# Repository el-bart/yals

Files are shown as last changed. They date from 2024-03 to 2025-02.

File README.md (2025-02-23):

# YALS: Yet Another Linear Servo

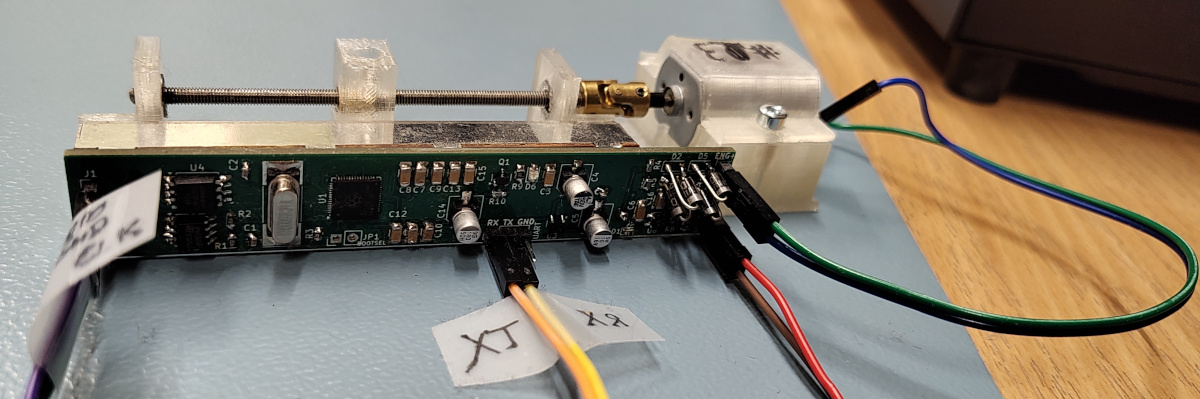
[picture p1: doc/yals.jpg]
YALS 1st prototype


project to build a linear servo for RC models.

## key project assumptions

* long move range
* digital position control
* digital feedback on current servo position
* 12V power supply (directly from battery)
* does not consume power when not moving, while still keeping position
* possible magnetic coupling with element moved
* programmable and persistent:
  * min / max positions
  * LED brightness

## building

TL;DR just run `make` from project's root directory.

toolchain has been dockerized.
to make usage more convenient, there's a top-level `Makefile` to run all the elements.
it automatically keeps dependsncies in place.

generated stuff:
* 3D models for printing:
  * all in: `body/build/voron_24_revo/petg/strength/*.gcode`
  * note that there can be >1 carriage to choose from
* electronics (HW):
  * gerber files for PCB: `board/hw/build/gerber.zip`
  * PCB assembly: `board/hw/build/graphics/`
  * BOM: `board/hw/build/bom.csv`
* software (SW):
  * to flash use `./rp2020_sdk rp2040_flash <name_of_binary.elf>` from `board/sw` directory
  * binaries:
    * controller to flash (production): `board/sw/build/rp2040/servo_ctrl.elf`
    * manual tests (for validation of HW assembly):
      * `board/sw/build/rp2040/Hal/rp2040/Hal_*.mtest.elf`
      * `board/sw/build/rp2040/Utils/*.mtest.elf`

## assembly

### BOM
* 1x PCB assembly (see `baord/hw` - build it to get `board/hw/build/bom.csv`)
* 1x MT44 DC motor
* 2x 3x7x3mm ball bearing
* 1x 3mm-3mm universal joing (aka: Cardan joint)
* 1x 3mm threaded rod (~12cm)
* 3x 3mm threaded inset (1x for carriage and 2x for engine)
* 2x M3x14 screws (engine mount)
* 2x M3x10 screws (potentiometer mount)

### tools
* soldering iron
* 3D printer for YALS' body
* hex-key set
* pico-probe or raspberry pi SBC to flash `rp2040` µC

## FAQ

### why no position-watchdog?
µC has internal watchdog, that kicks in in case software gets stuck.

however there's no application-level watchdog (e.g. a dedicated command that'd require a new command reception in a given time)
as servo does not go bonkers when signal is lost (as typical, cheap, analog do).
instead it keeps current position effortlessly.
on start, current position is retained as well.
therefor there's no need to perform any special actions, when no new command is received.

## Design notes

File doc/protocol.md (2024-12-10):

# protocol definition

communication protocol definition, used to communicate with the YALS device.
it consists of 1-line commands and responses and ends with checksum.
line ends with a new-line character (`\n` or `\r`).

consecutive new-line characters are ignored.

despite of being ASCII-printable, for ease of parsing, each command is fixed-width.
this means that values might need to be `0`-padded.

## checksum

checksum is calculated as a bit XOR of all bytes of the source frame.
checksum is hex-encoded.

example checksum of 3 bytes of data (here as hex): `0xFF 0x42 0x10`  is equal to:
`0xFF ^ 0x42 ^ 0x10`.
note that new-line characters are not part of checksum.

checksum is optional.
a literal string `XX` can be used to indicate it's not set and should not be checked.
this is mostly for debugging purposes - it should never be used in production!

## protocol

### ping
#### request
```
~XX\n
```
where:
* `XX` is hex-encoded checksum (or literal `XX` - meaning unset)
#### reply
* OK: `+msgXX\n` where:
  * `msg` is a string containing basic device info (name, version, etc.). 30B max.
  * `XX` is hex-encoded checksum
* error: `-msgXX\n` where:
  * `msg` is an error description string. 30B max.
  * `XX` is hex-encoded checksum

### set servo position
#### request
```
@nnnXX\n
```
where:
* `nnn` is servo position in 000..999 range
* `XX` is hex-encoded checksum (or literal `XX` - meaning unset)
#### reply
* OK: `+XX\n`
  * `XX` is hex-encoded checksum
* error: `-msgXX\n` where:
  * `msg` is a string containing basic device info (name, version, etc.). 30B max.
  * `XX` is hex-encoded checksum

### get servo position
#### request
```
!XX\n
```
where:
* `XX` is hex-encoded checksum (or literal `XX` - meaning unset)
#### reply
* OK: `+nnnXX\n` where:
  * `nnn` is a current 000..999 servo position
  * `XX` is hex-encoded checksum
* error: `-msgXX\n` where:
  * `msg` is a string containing basic device info (name, version, etc.). 30B max.
  * `XX` is hex-encoded checksum

### set min servo position
#### request
```
<nnnXX\n
```
where:
* `nnn` is 000...999 position
* `XX` is hex-encoded checksum (or literal `XX` - meaning unset)
#### reply
* OK: `+XX\n`
  * `XX` is hex-encoded checksum
* error: `-msgXX\n` where:
  * `msg` is a string containing basic device info (name, version, etc.). 30B max.
  * `XX` is hex-encoded checksum

### set max servo position
#### request
```
>nnnXX\n
```
where:
* `nnn` is 000...999 position
* `XX` is hex-encoded checksum (or literal `XX` - meaning unset)
#### reply
* OK: `+XX\n`
  * `XX` is hex-encoded checksum
* error: `-msgXX\n` where:
  * `msg` is a string containing basic device info (name, version, etc.). 30B max.
  * `XX` is hex-encoded checksum

### set LED brightness
#### request
```
*nnXX\n
```
where:
* `nn` is 00...99 LED brightness
* `XX` is hex-encoded checksum (or literal `XX` - meaning unset)
#### reply
* OK: `+XX\n`
  * `XX` is hex-encoded checksum
* error: `-msgXX\n` where:
  * `msg` is a string containing basic device info (name, version, etc.). 30B max.
  * `XX` is hex-encoded checksum

### get telemetry
#### request
```
#XX\n
```
where:
* `XX` is hex-encoded checksum (or literal `XX` - meaning unset)
#### reply
* OK: `+IiiiiUuuuuuXX\n` where:
  * `iiii` is current engine current in `mA` (0000..9999); e.g. `1234` is 1.234 A.
  * `uuuuu` is current main voltage in `mV` (00000..99999); e.g. `12345` is 12.345 V.
  * `XX` is hex-encoded checksum
* error: `-msgXX\n` where:
  * `msg` is a string containing basic device info (name, version, etc.). 30B max.
  * `XX` is hex-encoded checksum

### get persistent configuration
#### request
```
?XX\n
```
where:
* `XX` is hex-encoded checksum (or literal `XX` - meaning unset)
#### reply
* OK: `+<mmm>MMM*bbXX\n` where:
  * `mmm` is 000..999 servo min position
  * `MMM` is 000..999 servo max position
  * `bb` is 00..99 LED brightness
  * `XX` is hex-encoded checksum
* error: `-msgXX\n` where:
  * `msg` is a string containing basic device info (name, version, etc.). 30B max.
  * `XX` is hex-encoded checksum

### cheatsheet

this section is a brief summary of the whole section.
it's based on examples with 1-liner explanation.

all `XX` characters should be replaced with checksum, or can be taken literally (i.e. no checksum).
replies also ommit checksums.

* ping / get version info:
  * request: `~XX\n`
  * reply: `YALS v1.2.3-42-abcedfXX\n`
* set servo position to `98`
  * request: `@098XX\n`
  * reply: `+XX\n`
* return servo position (set to `098`)
  * request: `!XX\n`
  * reply: `+098XX\n`
* set servo minimum position to `200`:
  * request: `<200XX\n`
  * reply: `+XX\n`
* set servo maximum position to `800`:
  * request: `>800XX\n`
  * reply: `+XX\n`
* set LED birghtness to `42`:
  * request: `*42XX\n`
  * reply: `+XX\n`
* get telemetry:
  * request: `#XX\n`
  * reply: `+I01234U12345XX\n` (i.e. 0.1234 A and 12.345 V
* get persisted configuration:
  * request: `?XX\n`
  * reply: `+<200>800*42XX\n` (i.e. pos limits are 200..800, LED brightness is 42)

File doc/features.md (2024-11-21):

# features

## startup
* moving servo to within min..max range on init
* setting LED brightness

## protocol
* simple, ASCII-based serial protocol for I/O
* getting and setting:
  * servo position
  * min/max positions range for servo (preserved across restarts)
* readout:
  * SW information
  * telemetry (Vcc, engine current)

## misc
* hard min/max limits, compensating for potentiometer inaccuracies

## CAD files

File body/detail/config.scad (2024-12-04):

include <../m3d/engine/dc/mt44_conf.scad>

// CDE23N-60-B50K linear potentiometer (horizontal, on side, knob to the right)
lin_pot_travel = 60;
lin_pot_size = [11, lin_pot_travel+28.3, 13];
lin_pot_mount_screw_d = 3;
lin_pot_mount_screw_dist_from_edge = ( lin_pot_size.y - lin_pot_travel - 20 ) / 2;
lin_pot_mount_screw_pos = [4, lin_pot_size.y-4];
lin_pot_knob_size = [15.3, 5, 1.2];
lin_pot_knob_dist_from_edge = ( lin_pot_size.y - lin_pot_travel ) / 2;
lin_pot_knob_pos_range = [lin_pot_knob_dist_from_edge, lin_pot_size.y - lin_pot_knob_dist_from_edge];

// MT44 engine - mock sizes taken from m3d
engine_box_size = engine_dc_mt44_box_size;
engine_size_shaft_d = engine_dc_mt44_shaft_d;
engine_size_shaft_h = engine_dc_mt44_shaft_h + engine_dc_mt44_bearing_top_h;
engine_size_total_len = engine_box_size.z + engine_size_shaft_h;

// universal joint
universal_joint_part_bottom_h = 2.8;
universal_joint_part_top_h = 8.75;
universal_joint_part_joint_h = 6.5;
universal_joint_full_len = 2 * universal_joint_part_joint_h;
universal_joint_d = 7;
universal_joint_shaft_d = 3;
universal_joint_wall = 1;
assert( universal_joint_shaft_d + 2*universal_joint_wall <= universal_joint_d );
universal_joint_center_spacing = universal_joint_part_joint_h - universal_joint_part_bottom_h; // distance to be kept from the center of the joint

// screw row
screw_rod_d = 3;

// servo body
servo_body_bottom_h = 2;
servo_body_wall = 2;
servo_body_mount_screw_d = 3;
servo_body_threaded_insert_slot_d = 4.6;
servo_body_threaded_insert_slot_h = 5.7;
servo_body_engine_mount_spacing_r = 0.15; // around the engine
servo_body_engine_mount_spacing_h = 0.15; // before and after engine (dy)

// bearing size [mm]
bearing_size = [3, 7, 3]; // [ internal_d, external_d, h ]

// combined, utility metrics
base_to_axis_h = servo_body_bottom_h + lin_pot_size.z;

// servo body: mount tower dimensions
servo_body_mount_tower_hole_dist_to_wall = 3;
servo_body_mount_tower_size = ( servo_body_mount_screw_d + 2 * servo_body_mount_tower_hole_dist_to_wall ) * [1,1,0] +
                              [ 0,0, base_to_axis_h +
                                engine_box_size.y/2 +
                                servo_body_engine_mount_spacing_r +
                                servo_body_wall ];

// carriage
carriage_magnet_d = 5;
carriage_magnet_h = 5;
carriage_wall = 2;
carriage_knob_slot_spacing = 0.5;
carriage_rod_h = carriage_wall + (carriage_knob_slot_spacing + lin_pot_knob_size.z)/2 + // center to potentiometer's knob center
                 base_to_axis_h - servo_body_bottom_h - lin_pot_size.z/2;               // move to height of the rod
carriage_size = [ 10,
                  lin_pot_knob_size.y + 2*carriage_wall,
                  carriage_rod_h + screw_rod_d/2 + carriage_wall + carriage_magnet_h ];
carriage_threaded_insert_slot_d = 4.6;
carriage_threaded_insert_slot_h = 5.7;

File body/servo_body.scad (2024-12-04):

use <mock/lin_pot.scad>
use <mock/bearing.scad>
use <mock/universal_joint.scad>
use <mock/pcb.scad>
use <servo_body_top_mount.scad>
use <carriage.scad>
use <m3d/fn.scad>
use <m3d/engine/dc/mt44.scad>
include <m3d/math.scad>
include <detail/config.scad>

module engine()
{
  engine_dc_mt44();
}

module engine_crosssecion_2d()
{
  engine_dc_mt44_crosssection_2d();
}


module servo_body_engine_pos()
{
  translate([0, -engine_size_total_len - universal_joint_center_spacing, base_to_axis_h]) // axis-centered
    rotate([-90, 0, 0])
      children();
}


module servo_body_lin_pot_pos()
{
  translate([0, 0, servo_body_bottom_h])
    translate([-lin_pot_knob_size.x/2, 0, -lin_pot_size.z/2]) // mount position
      translate([-lin_pot_size.x, 0, lin_pot_size.z/2]) // axis-centered
        children();
}


module servo_body_pcb_pos()
{
  translate([-5, -14.3, -servo_body_bottom_h+1])
    servo_body_lin_pot_pos()
      children();
}


module servo_body_universal_joint_pos()
{
  translate([0, -universal_joint_full_len/2, base_to_axis_h])
    rotate([-90, 0, 0])
      children();
}


module servo_body_carriage_pos()
{
  knob_center = lin_pot_knob_pos_range[0] + (lin_pot_knob_pos_range[1] - lin_pot_knob_pos_range[0]) / 2;
  translate([ lin_pot_size.x + lin_pot_knob_size.x/2,
              knob_center,
              lin_pot_size.z/2 - lin_pot_knob_size.z/2 - carriage_wall - carriage_knob_slot_spacing/2 ]) // move to final spot
    translate([-carriage_size.x/2, -carriage_size.y/2, 0]) // center
      servo_body_lin_pot_pos()
        children();
}


module servo_body_mount_tower_center_pos()
{
  w = servo_body_mount_tower_size.x;

  // around engine
  sbw = servo_body_wall;
  screw_mount_space = sbw + servo_body_threaded_insert_slot_d + sbw;
  engine_base_plate_y = engine_size_total_len + universal_joint_center_spacing + sbw;
  for(dx=[-1, +1])
    translate([ dx*(engine_box_size.x + 2*screw_mount_space)/2,
                -engine_base_plate_y + sbw,
                0 ])
      translate([dx*w/2, w/2, 0])
        children();

  // end of cariage
  for(dx=[-1, +1])
    translate([dx*w/2, lin_pot_size.y, 0])
      translate([0, w/2, 0])
        rotate([0, 0, 90])
          children();
}


module servo_body(mocks=true)
{
  module mount_tower()
  {
    d2w = servo_body_mount_tower_hole_dist_to_wall;
    size = servo_body_mount_tower_size;
    w = size.x;
    assert(size.x == size.y);
    h = size.z;

    translate(-w/2*[1,1,0])
      difference()
      {
        $fn=fn(30);
        ssd = servo_body_mount_screw_d + 0.5; // screw slot diameter

        cube(size);
        // top-down screw
        translate([w/2, w/2, -eps])
          cylinder(d=ssd, h=h+2*eps);
        // front-back screws (top and bottom)
        translate([0, -eps, 0])
          rotate([-90, 0, 0])
            for(dy=[ssd/2 + d2w, h - ssd/2 - d2w])
              translate([w/2, -dy, 0])
                cylinder(d=ssd, h=w+2*eps);
      }
  }

  module main_support()
  {
    lps = lin_pot_size;
    ks = lin_pot_knob_size;
    bh = servo_body_bottom_h;
    thickness = 3.5;

    module lin_pot_screw_mounts()
    {
      module blocks()
      {
        module lin_pot_screw_mount()
        {
          s = [thickness, lin_pot_knob_pos_range[0]-lin_pot_knob_size.y/2, lin_pot_size.z];

          module phased_cube(size, phase)
          {
            translate([0, size.y, 0])
              rotate([90, 0, 0])
                linear_extrude(size.y)
                  polygon([
                    [0, 0],
                    [0, size.z],
                    [size.x - phase[0], size.z],
                    [size.x,            size.z - phase[1]],
                    [size.x, 0],
                  ]);
          }

          phased_cube(size=s, phase=[2/3*s.x, s.x]);
        }

        for(dy=[0, lin_pot_knob_pos_range[1]+ks.y/2])
          translate([lin_pot_size.x, dy, 0])
            servo_body_lin_pot_pos()
              lin_pot_screw_mount();
      }

      difference()
      {
        blocks();
        // screw holes
        for(dy=lin_pot_mount_screw_pos)
          translate([-eps+lin_pot_size.x, dy, lin_pot_size.z/2])
            servo_body_lin_pot_pos()
              rotate([0, 90, 0])
                cylinder(d=lin_pot_mount_screw_d+0.75, h=thickness+2*eps, $fn=fn(50));
      }
    }

    module bearing_support()
    {
      h = base_to_axis_h - servo_body_bottom_h + bearing_size[1]/2 + thickness;
      s = [lin_pot_knob_size.x, thickness, h];
      pos = lin_pot_knob_pos_range + [-s.y-lin_pot_knob_size.y/2, lin_pot_knob_size.y/2];

      module support()
      {
        difference()
        {
          cube(s);
          translate([s.x/2, -eps, base_to_axis_h-servo_body_bottom_h])
          {
            // rod
            rotate([-90, 0, 0])
              cylinder(d=screw_rod_d+1, h=s.y+2*eps, $fn=fn(40));
            rotate([-90, 0, 0])
              bearing_slot();
          }
        }
      }

      translate([-s.x/2, 0, servo_body_bottom_h])
      {
        // supports
        for(dy=pos)
          translate([0, dy, 0])
            support();
        // stiffners
        ss = [thickness, pos[1]-pos[0], thickness/2];
        for(dx=[0, s.x-ss.x])
          translate([dx, pos[0], 0])
            cube(ss);
      }
    }

    module engine_support()
    {
      wall = servo_body_wall;
      es = [ engine_box_size.x, engine_box_size.z, engine_box_size.y ];
      screw_mount_space = wall + servo_body_threaded_insert_slot_d + wall;
      sb = [ es.x + 2*screw_mount_space,
             engine_size_total_len + universal_joint_center_spacing + wall,
             servo_body_bottom_h ];

      module base_engine_mount()
      {
        to_eng_base = base_to_axis_h - servo_body_bottom_h - es.z/2;
        eng_sup = [ sb.x, es.y, base_to_axis_h - servo_body_bottom_h ];

        module support_block()
        {
          module core()
          {
            // engine block holder
            translate([0, wall, 0 ])
            {
              cube(eng_sup);
            }
            // engine-blocking elements
            union()
            {
              sblk = wall*[1,1,0] + [0, 0, to_eng_base+wall];
              for(dy=[0, wall + es.y])
                translate([sb.x/2-sblk.x/2, dy, 0])
                  cube(sblk);
            }
          }

          translate(-[sb.x/2, sb.y, 0])
          {
            delta_y = servo_body_engine_mount_spacing_h;
            // base
            cube(sb);
            // elements on top
            translate([0, 0, servo_body_bottom_h])
            {
              difference()
              {
                core();
                translate([sb.x/2, wall-delta_y, base_to_axis_h-servo_body_bottom_h])
                  spaced_engine_slot(dy=2*delta_y);
              }
            }
          }
        }

        module threaded_insert_slot(h)
        {
          rotate([180, 0, 0])
          {
            cylinder(d=servo_body_threaded_insert_slot_d,
                     h=servo_body_threaded_insert_slot_h,
                     $fn=fn(20));
            translate([0, 0, servo_body_threaded_insert_slot_h-eps])
              cylinder(d=servo_body_mount_screw_d+0.5, h=h+eps, $fn=fn(40));
          }
        }

        difference()
        {
          support_block();
          for(dy=[-1,+1])
            translate([ dy*(sb.x/2-servo_body_threaded_insert_slot_d/2-wall),
                        -sb.y + wall + es.y/2,
                        base_to_axis_h+eps ])
              threaded_insert_slot(h=base_to_axis_h);
        }
      }

      base_engine_mount();
    }

    // base
    translate([-lps.x - ks.x/2, 0, 0])
      cube([lps.x + ks.x, lps.y, bh]);
    lin_pot_screw_mounts();
    bearing_support();
    engine_support();
    // mount holes
    servo_body_mount_tower_center_pos()
      mount_tower();
  }

  main_support();

  %if(mocks)
    translate([0, universal_joint_center_spacing, base_to_axis_h])
      rotate([-90, 0, 0])
        cylinder(d=screw_rod_d,
                 h=lin_pot_size.y-universal_joint_center_spacing,
                 $fn=fn(40)); // main rod
  %if(mocks)
    servo_body_lin_pot_pos()
    {
      lin_pot(  0/*%*/);
      lin_pot( 50/*%*/);
      lin_pot(100/*%*/);
    }
  %if(mocks)
    servo_body_engine_pos()
      engine();
  %if(mocks)
    servo_body_universal_joint_pos()
      universal_joint();
  %if(mocks)
    translate([0, -eps, 0])
      servo_body_engine_pos()
        rotate([90, 0, 0])
          servo_body_top_mount();
  %if(mocks)
    servo_body_carriage_pos()
      carriage();
  %if(mocks)
    servo_body_pcb_pos()
      pcb();
}


servo_body();

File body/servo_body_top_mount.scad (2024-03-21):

use <m3d/fn.scad>
use <m3d/engine/dc/mt44.scad>
include <m3d/math.scad>
include <detail/config.scad>


module spaced_engine_slot(dy=0, spacing=servo_body_engine_mount_spacing_r)
{
  rotate([-90, 0, 0])
    linear_extrude(engine_box_size.z + dy)
      offset(r=spacing)
        engine_dc_mt44_crosssection_2d($fn=fn(100));
}


module servo_body_top_mount()
{
  wall = servo_body_wall;
  lenght = engine_box_size.z;
  es = [ engine_box_size.x, engine_box_size.z, engine_box_size.y ];
  base_size = [ es.x+2*(2*wall+servo_body_threaded_insert_slot_d), es.y, wall ];
  screw_d = servo_body_mount_screw_d + 0.5;

  module core()
  {
    module block()
    {
      spaced_engine_slot(dy=0, spacing=wall+servo_body_engine_mount_spacing_r);
      translate([-base_size.x/2, 0, 0])
        cube(base_size);
    }

    difference()
    {
      block();
      // hollow body
      translate([0, -eps, 0])
        spaced_engine_slot(dy=2*eps);
      // remove bottom part
      cut = [2*(es.x + 2*wall), lenght+2*eps, es.z];
      translate(-[cut.x/2, eps, cut.z])
        cube(cut);
    }
  }

  difference()
  {
    core();
    // screw holes
    for(dx=[-1,+1])
      translate([dx*(base_size.x/2 - screw_d/2 - wall), lenght/2, -eps])
        cylinder(d=screw_d, h=wall+2*eps, $fn=fn(50));
  }
}


rotate([90, 0, 0])
  servo_body_top_mount();

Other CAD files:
body/carriage.scad
body/m3d/all.scad
body/m3d/engine/dc/mt44.scad
body/m3d/engine/dc/mt44_conf.scad
body/m3d/engine/dc/mt83.scad
body/m3d/engine/dc/mt83_conf.scad
body/m3d/engine/stepper/nema17.scad
body/m3d/fn.scad
body/m3d/inner_shell.scad
body/m3d/map.scad
body/m3d/math.scad
body/m3d/nema17_stepper.scad
body/m3d/outer_shell.scad
body/m3d/rounded_cube.scad
body/m3d/screw_head_hex.scad
body/m3d/threaded_inserts/cnc_kitchen.scad
body/mock/bearing.scad
body/mock/lin_pot.scad
body/mock/pcb.scad
body/mock/universal_joint.scad

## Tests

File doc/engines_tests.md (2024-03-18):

# engines tests

sumary of all tested engines.

| type | speed | stuck-at-end | stall current | running current | price |
|---|---|---|---|---|---|
| MT83 | good  | yes :( | 2 A | 0.7 A | 1.5 EUR |
| MT44 | good  | yes :( | 0.6 A | 0.25 A | 3.7 EUR |
| MT78 | good  | yes :( | 0.8 A | 0.3 A | 1.6 EUR |
| johnson 10435 | slow  | yes :( | 0.2 A | 0.1 A | 1.6 EUR |

inital model (v0.1) was prepared for MT83 engine.
it is however too power-hungry, especially at stall.

johnson 10435 is far too weak for this application.
it is rejected.

MT44 and MT78 were performing similar, but MT44 is consuming 25% less power.
therefor MT44 is the winner.

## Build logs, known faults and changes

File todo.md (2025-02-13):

# TODO list

## 3D model
* add end-stops (or otherwise guarantee never going out of bounds, as it stalls engine and permanently locks it, requiring manual intervention)
  - this should be doable with potentiometer and moving slow ("calibration phase"?)
* add "left" and "right" visual markers on servo edges, to signal cardinal directions

## board
* silkscreen:
  * describe each SWD pin
  * add board version
* pull-up `picorun` to Vcc
* add 3.3V in next to SWD (for ease of programming w/o external power supply)
* consider switching to hand-soldering pads for elements
* add polymer fuse for power line
* consider using JST XH2.5 for power and communication (1 plug, 4 pins?) and soldering engine wires directly

## software
* native client library to use servo with demo using serial port
* LED blinking when I/Oing (on command level)
* PID controller:
  * fine-tune PID to avoid overshoots when traveling long distance
  * make PID default for full range of travel

## bugs:

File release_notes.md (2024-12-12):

# release notes

## dev

## v0.4
* added screw holes to mount servo to the external element
* persisting values in EEPROM is now operational
* added full sanitization of the EEPROM-read values
* EEPROM writes simplified

## v0.3
* saves current when servo is at the destination
* software implementation:
  * PID-based control loop
  * compact, ASCII-based communication protocol
    * getting and setting sevo position
  * Watchdog support
  * Serial I/O (UART) with buffering
  * 250Hz control loop (I/O is handled real time)
  * hardware-based limits for travel movement, to avoid hitting hard stops
  * feedback for:
    * supply voltage (Vcc)
    * current consumption from engine
  * LED dimming
* docker-based SDK for:
  * 3D body (OpenSCAD)
  * electronics (KiCad)
  * software (C++)

## v0.2
* new body designed around `MT44` engine
* electronics design
* first PCB version sent for manufacturing
* designed so that it's not back-drivable

## v0.1
* 3D model for body (designed for `MT83` engine)

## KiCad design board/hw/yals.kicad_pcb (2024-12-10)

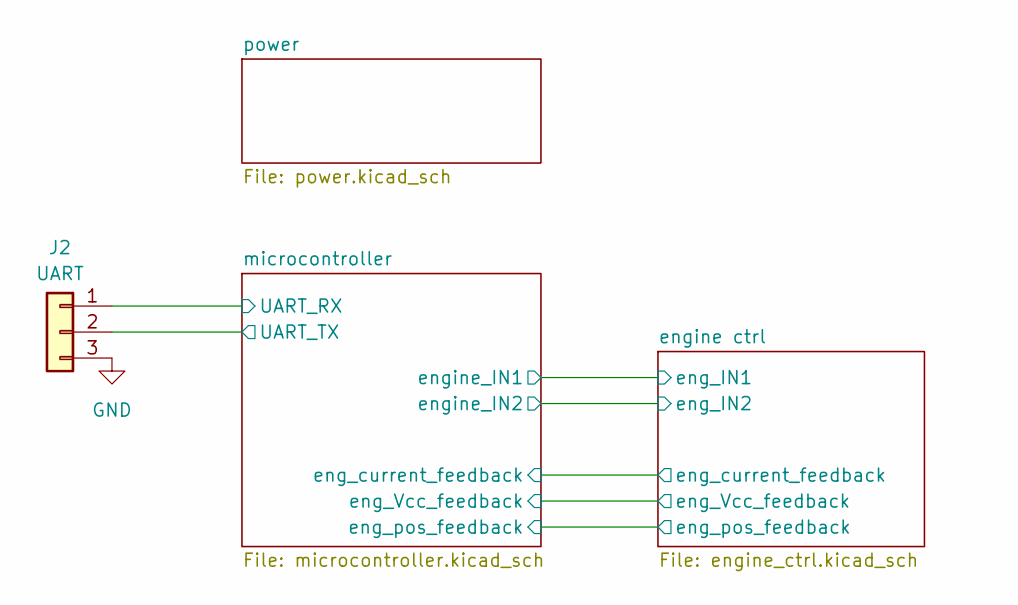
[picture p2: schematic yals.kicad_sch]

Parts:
J2: UART; PinHeader_1x03_P2.54mm_Vertical

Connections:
/microcontroller/UART_RX: J2.1; also elsewhere on the board
/microcontroller/UART_TX: J2.2; also elsewhere on the board
GND: J2.3; also elsewhere on the board

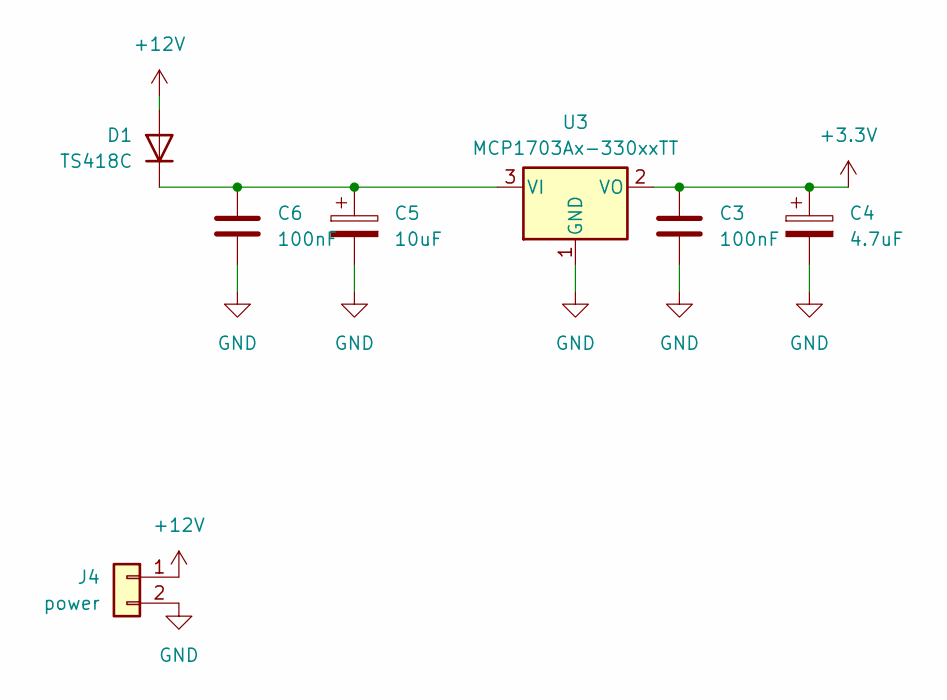
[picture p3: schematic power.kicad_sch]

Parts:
C3, C6: 100nF; C_1206_3216Metric
C4: 4.7uF; CP_Elec_5x4.5
C5: 10uF; CP_Elec_5x4.5
D1: TS418C; D_0603_1608Metric
J4: power; PinHeader_1x02_P2.54mm_Vertical
U3: MCP1703Ax-330xxTT; SOT-23

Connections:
+3.3V: C3.1, C4.1, U3.2 (VO); also elsewhere on the board
+12V: D1.2 (A), J4.1; also elsewhere on the board
GND: C3.2, C4.2, C5.2, C6.2, J4.2, U3.1 (GND); also elsewhere on the board
unnamed: C5.1, C6.1, D1.1 (K), U3.3 (VI)

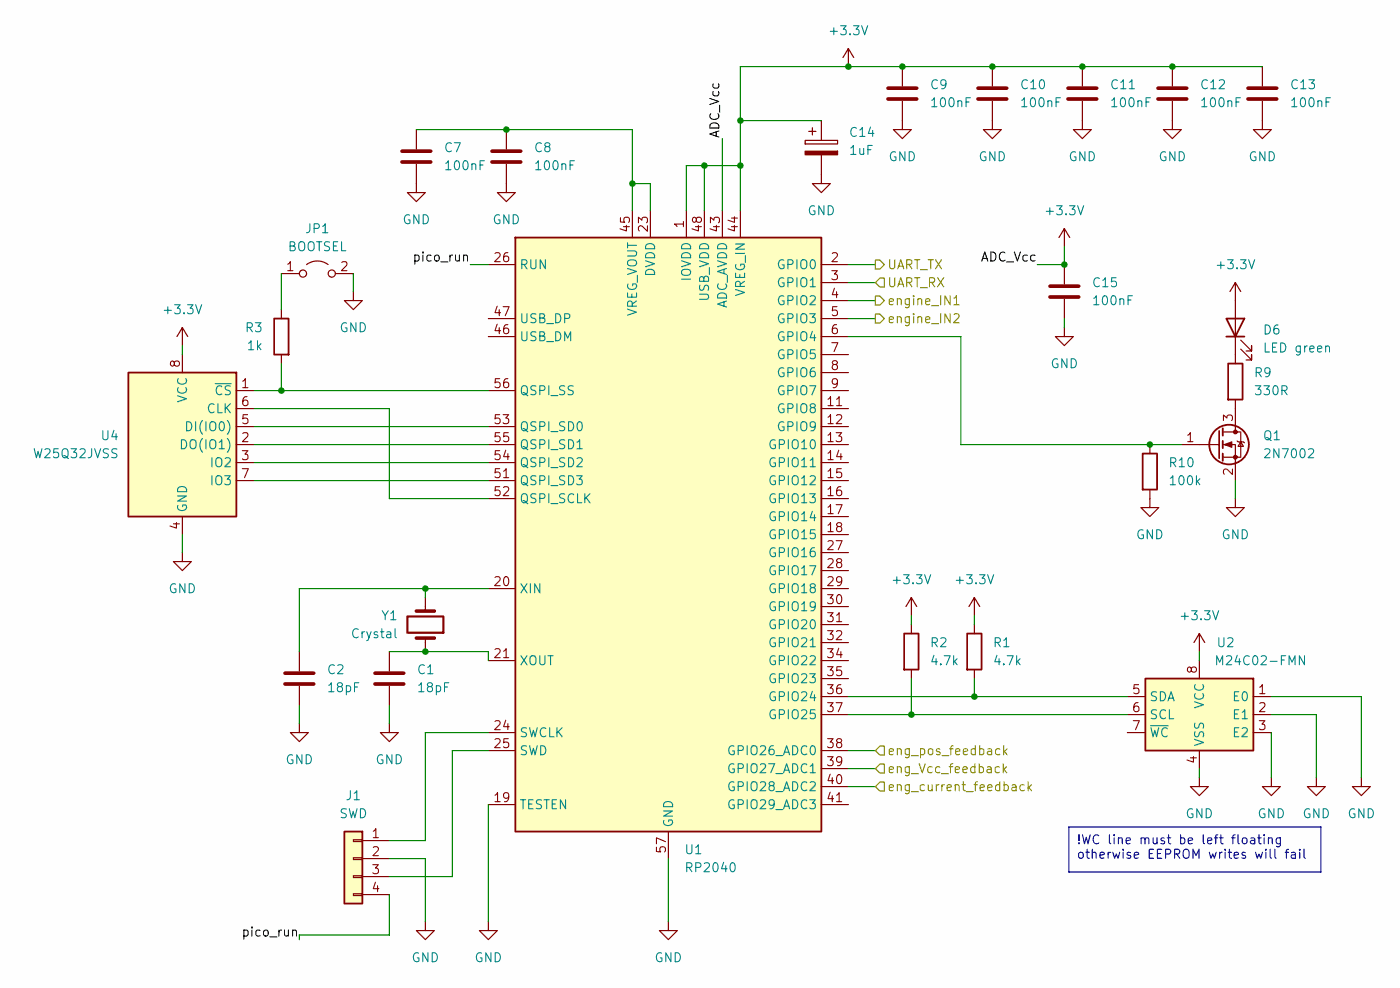
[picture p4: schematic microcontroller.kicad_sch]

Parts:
C1, C2: 18pF; C_0603_1608Metric
C7, C8, C9, C10, C11, C12, C13, C15: 100nF; C_1206_3216Metric
C14: 1uF; CP_Elec_5x4.5
D6: LED green; LED_0805_2012Metric_Pad1.15x1.40mm_HandSolder
J1: SWD; PinHeader_1x04_P2.54mm_Vertical
JP1: BOOTSEL; PinHeader_1x02_P2.54mm_Vertical
Q1: 2N7002; SOT-23
R1, R2: 4.7k; R_0603_1608Metric
R3: 1k; R_0603_1608Metric
R9: 330R; R_0805_2012Metric
R10: 100k; R_0603_1608Metric
U1: RP2040; QFN-56-1EP_7x7mm_P0.4mm_EP3.2x3.2mm
U2: M24C02-FMN; SOIC-8_3.9x4.9mm_P1.27mm
U4: W25Q32JVSS; SOIC-8_5.23x5.23mm_P1.27mm
Y1: Crystal; Crystal_SMD_SeikoEpson_MA505-2Pin_12.7x5.1mm

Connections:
+3.3V: C9.1, C10.1, C11.1, C12.1, C13.1, C14.1, C15.1, D6.2 (A), R1.1, R2.1, U1.1 (IOVDD), U1.10 (IOVDD), U1.22 (IOVDD), U1.33 (IOVDD), U1.42 (IOVDD), U1.43 (ADC_AVDD), U1.44 (VREG_IN), U1.48 (USB_VDD), U1.49 (IOVDD), U2.8 (VCC), U4.8 (VCC); also elsewhere on the board
/engine ctrl/eng_IN1: U1.4 (GPIO2); also elsewhere on the board
/engine ctrl/eng_IN2: U1.5 (GPIO3); also elsewhere on the board
/engine ctrl/eng_Vcc_feedback: U1.39 (GPIO27_ADC1); also elsewhere on the board
/engine ctrl/eng_current_feedback: U1.40 (GPIO28_ADC2); also elsewhere on the board
/engine ctrl/eng_pos_feedback: U1.38 (GPIO26_ADC0); also elsewhere on the board
/microcontroller/UART_RX: U1.3 (GPIO1); also elsewhere on the board
/microcontroller/UART_TX: U1.2 (GPIO0); also elsewhere on the board
/microcontroller/pico_run: J1.4, U1.26 (RUN)
GND: C1.2, C2.2, C7.2, C8.2, C9.2, C10.2, C11.2, C12.2, C13.2, C14.2, C15.2, J1.2, JP1.2 (B), Q1.2 (S), R10.2, U1.19 (TESTEN), U1.57 (GND), U2.1 (E0), U2.2 (E1), U2.3 (E2), U2.4 (VSS), U4.4 (GND); also elsewhere on the board
unnamed: D6.1 (K), R9.1
unnamed: J1.1, U1.24 (SWCLK)
unnamed: J1.3, U1.25 (SWD)
unnamed: JP1.1 (A), R3.1
unnamed: Q1.3 (D), R9.2
unnamed: Q1.1 (G), R10.1, U1.6 (GPIO4)
unnamed: R1.2, U1.36 (GPIO24), U2.5 (SDA)
unnamed: R2.2, U1.37 (GPIO25), U2.6 (SCL)
unnamed: U1.52 (QSPI_SCLK), U4.6 (CLK)
unnamed: U1.53 (QSPI_SD0), U4.5 (DI(IO0))
unnamed: U1.55 (QSPI_SD1), U4.2 (DO(IO1))
unnamed: U1.54 (QSPI_SD2), U4.3 (IO2)
unnamed: U1.51 (QSPI_SD3), U4.7 (IO3)
unnamed: R3.2, U1.56 (QSPI_SS), U4.1 (~CS)
unnamed: C7.1, C8.1, U1.23 (DVDD), U1.45 (VREG_VOUT), U1.50 (DVDD)
unnamed: C2.1, U1.20 (XIN), Y1.2
unnamed: C1.1, U1.21 (XOUT), Y1.1

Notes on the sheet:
!WC line must be left floating otherwise EEPROM writes will fail

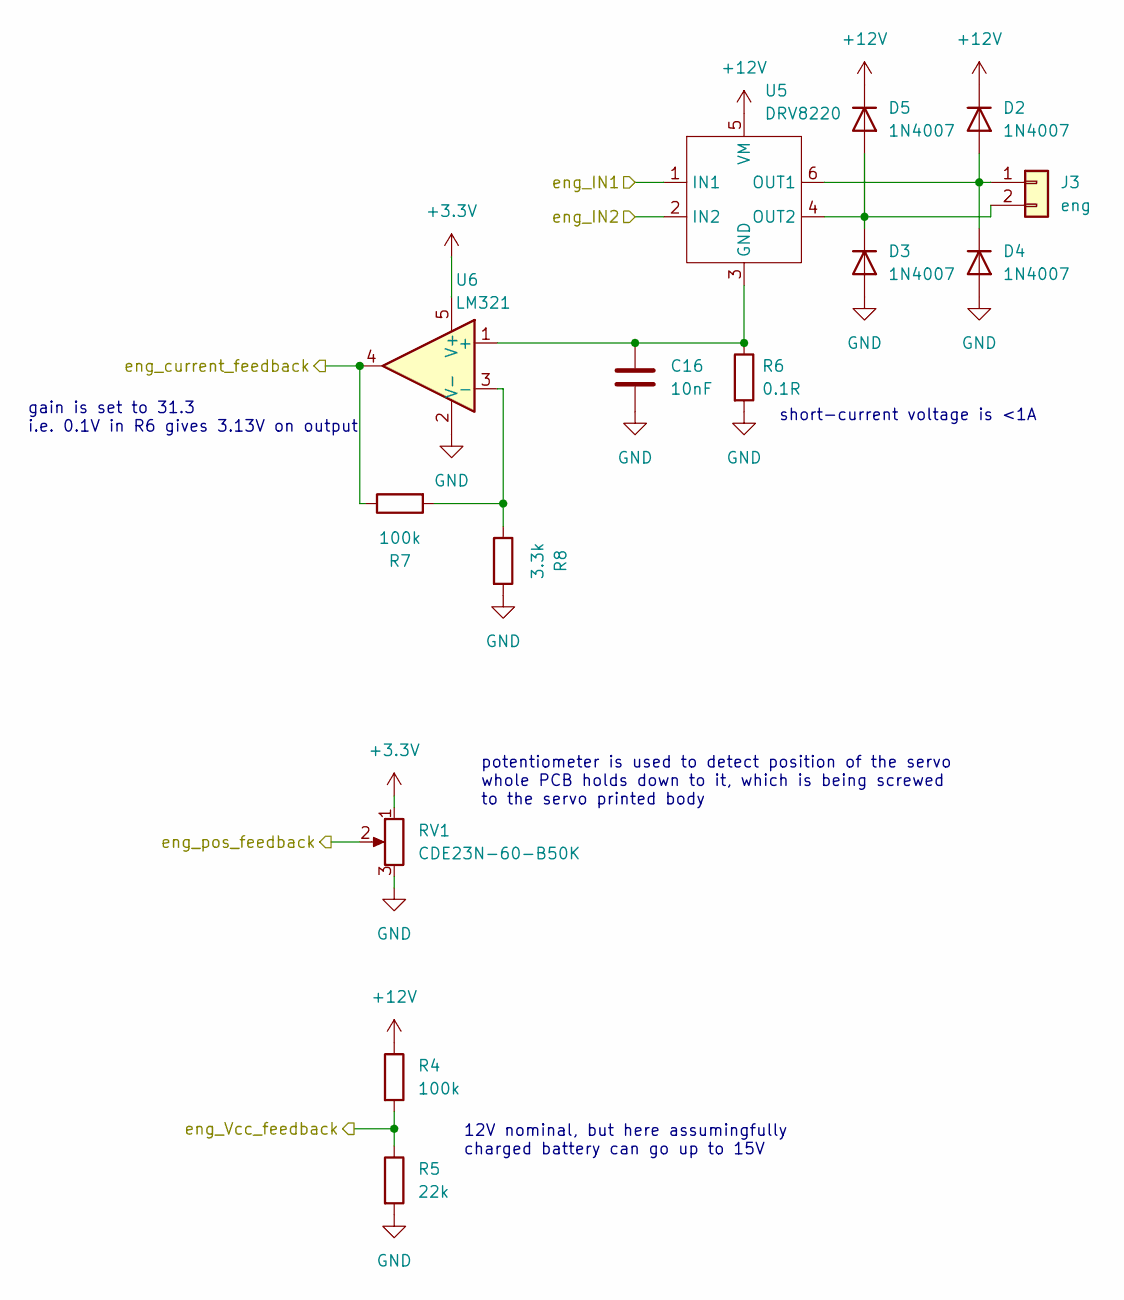
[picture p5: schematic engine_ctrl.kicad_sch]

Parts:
C16: 10nF; C_1206_3216Metric
D2, D3, D4, D5: 1N4007; D_SOD-123F
J3: eng; PinHeader_1x02_P2.54mm_Vertical
R4, R7: 100k; R_0603_1608Metric
R5: 22k; R_0603_1608Metric
R6: 0.1R; R_1206_3216Metric
R8: 3.3k; R_0603_1608Metric
RV1: CDE23N-60-B50K
U5: DRV8220; SOT-563
U6: LM321; SOT-23-5

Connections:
+3.3V: RV1.1, U6.5 (V+); also elsewhere on the board
+12V: D2.1 (K), D5.1 (K), R4.1, U5.5 (VM); also elsewhere on the board
/engine ctrl/eng_IN1: U5.1 (IN1); also elsewhere on the board
/engine ctrl/eng_IN2: U5.2 (IN2); also elsewhere on the board
/engine ctrl/eng_Vcc_feedback: R4.2, R5.1; also elsewhere on the board
/engine ctrl/eng_current_feedback: R7.1, U6.4; also elsewhere on the board
/engine ctrl/eng_pos_feedback: RV1.2; also elsewhere on the board
GND: C16.2, D3.2 (A), D4.2 (A), R5.2, R6.2, R8.2, RV1.3, U6.2 (V-); also elsewhere on the board
unnamed: D2.2 (A), D4.1 (K), J3.1, U5.6 (OUT1)
unnamed: D3.1 (K), D5.2 (A), J3.2, U5.4 (OUT2)
unnamed: C16.1, R6.1, U5.3 (GND), U6.1 (+)
unnamed: R7.2, R8.1, U6.3 (-)

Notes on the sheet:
short-current voltage is <1A
12V nominal, but here assumingfully charged battery can go up to 15V
potentiometer is used to detect position of the servo whole PCB holds down to it, which is being screwed to the servo printed body
gain is set to 31.3 i.e. 0.1V in R6 gives 3.13V on output

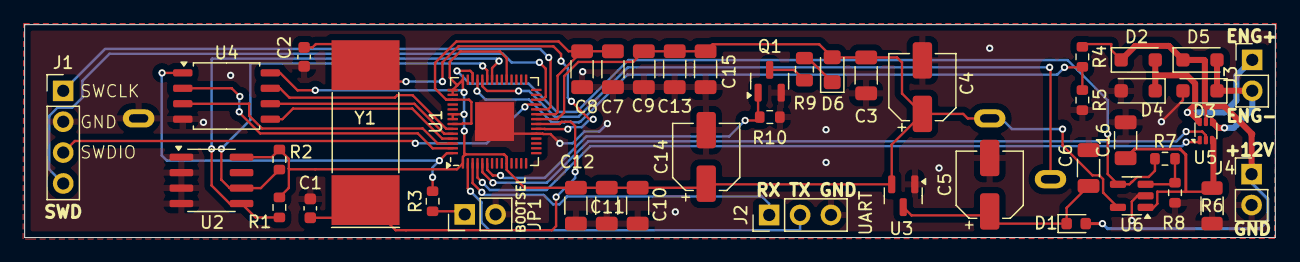
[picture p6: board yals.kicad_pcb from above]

Board: 2 copper layers, 102.9 x 17.5 mm, 46 parts (1 on the bottom side), 33 nets.

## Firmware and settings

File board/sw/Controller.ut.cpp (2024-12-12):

#include <catch2/catch.hpp>
#include "Controller.hpp"
#include "Hal/Sim.hpp"

using Hal::sim;
using namespace Utils::Config;

namespace
{

void enqueue_command(std::string_view cmd)
{
  // data
  for(auto c: cmd)
    sim().rx_.push_back(c);
  // no checksum
  sim().rx_.push_back('X');
  sim().rx_.push_back('X');
  // EOL
  sim().rx_.push_back('\n');
}

struct Reader
{
  std::string read_reply()
  {
    // make a copy to clear TX buffer so that more I/O can happen
    for(auto b: sim().tx_)
      received_.push_back(b);
    sim().tx_.clear();

    auto const eol = std::find( received_.begin(), received_.end(), '\n' );
    if( eol == received_.end() )
      return {};
    auto str = std::string{ received_.begin(), eol };
    received_.erase( received_.begin(), eol + 1 );

    if( str.size() < 3u )
      throw std::runtime_error{"read_reply(): line too short: " + str};

    // remove checksum
    if( not isxdigit( str.back() ) )
      throw std::runtime_error{"read_reply(): invalid checksum chracter at the end (1): " + str};
    str.pop_back();
    if( not isxdigit( str.back() ) )
      throw std::runtime_error{"read_reply(): invalid checksum chracter at the end (2): " + str};
    str.pop_back();

    return str;
  }

  std::deque<uint8_t> received_;
};


TEST_CASE("Controller's c-tor")
{
  sim().reset();
  sim().update(0.0);

  SECTION("on start current servo position is a new setpoint (i.e. do not move after start)")
  {
    Controller ctrl;
    CHECK( ctrl.context().setpoints_.position_ == Approx( sim().position_ ) );
  }

  SECTION("on start, if marker is not set, min and max positions as well as LED brightness are written to EEPROM")
  {
    sim().marker_clear();
    sim().min_position(0.4);
    sim().max_position(0.6);
    sim().EEPROM_LED_brightness(0.12);
    sim().position_ = 0.5;
    Controller ctrl;
    CHECK( sim().min_position() == Approx(servo_absolute_min) );
    CHECK( sim().max_position() == Approx(servo_absolute_max) );
    CHECK( sim().EEPROM_LED_brightness() == Approx(Utils::Config::default_LED_brightness) );
    CHECK( sim().marker_is_set() );
    CHECK( ctrl.context().setpoints_.min_pos_ == Approx( sim().min_position() ) );
    CHECK( ctrl.context().setpoints_.max_pos_ == Approx( sim().max_position() ) );
    CHECK( ctrl.context().setpoints_.LED_brightness_ == Approx( sim().EEPROM_LED_brightness() ) );
    CHECK( ctrl.context().setpoints_.LED_brightness_ == Approx( sim().LED_brightness_ ).margin(0.01)  );
  }

  SECTION("on start, if current servo setpoint is below min, it's clamped to it")
  {
    sim().min_position(0.7);
    sim().marker_set();
    sim().position_ = 0.5;
    Controller ctrl;
    CHECK( ctrl.context().setpoints_.position_ == Approx( sim().min_position() ) );
  }

  SECTION("on start, if current servo setpoint is above max, it's clamped to it")
  {
    sim().max_position(0.7);
    sim().position_ = 0.9;
    Controller ctrl;
    CHECK( ctrl.context().setpoints_.position_ == Approx( sim().max_position() ) );
  }

  SECTION("on start, sanitize EEPROM values")
  {
    sim().min_position(Utils::Config::servo_absolute_min);
    sim().max_position(Utils::Config::servo_absolute_max);
    sim().EEPROM_LED_brightness(Utils::Config::default_LED_brightness);
    sim().marker_set();
    sim().position_ = 0.5;

    SECTION("if min < 0.0")
    {
      sim().min_position(-0.1);
      Controller ctrl;
      // sanity checks
      CHECK( ctrl.context().setpoints_.min_pos_  <= ctrl.context().setpoints_.max_pos_  );
      CHECK( ctrl.context().setpoints_.min_pos_  <= ctrl.context().setpoints_.position_ );
      CHECK( ctrl.context().setpoints_.position_ <= ctrl.context().setpoints_.max_pos_  );
      // setpoints
      CHECK( ctrl.context().setpoints_.min_pos_        == Approx(Utils::Config::servo_absolute_min) );
      CHECK( ctrl.context().setpoints_.max_pos_        == Approx(Utils::Config::servo_absolute_max) );
      CHECK( ctrl.context().setpoints_.LED_brightness_ == Approx(Utils::Config::default_LED_brightness).margin(0.01) );
      CHECK( ctrl.context().setpoints_.position_       == Approx(0.5) );
      // EEPROM
      CHECK( sim().min_position()          == Approx(Utils::Config::servo_absolute_min) );
      CHECK( sim().max_position()          == Approx(Utils::Config::servo_absolute_max) );
      CHECK( sim().EEPROM_LED_brightness() == Approx(Utils::Config::default_LED_brightness).margin(0.01) );
    }

    SECTION("if min > 1.0")
    {
      sim().min_position(1.1);
      Controller ctrl;
      // sanity checks
      CHECK( ctrl.context().setpoints_.min_pos_  <= ctrl.context().setpoints_.max_pos_  );
      CHECK( ctrl.context().setpoints_.min_pos_  <= ctrl.context().setpoints_.position_ );
      CHECK( ctrl.context().setpoints_.position_ <= ctrl.context().setpoints_.max_pos_  );
      // setpoints
      CHECK( ctrl.context().setpoints_.min_pos_        == Approx(Utils::Config::servo_absolute_min) );
      CHECK( ctrl.context().setpoints_.max_pos_        == Approx(Utils::Config::servo_absolute_max) );
      CHECK( ctrl.context().setpoints_.LED_brightness_ == Approx(Utils::Config::default_LED_brightness).margin(0.01) );
      CHECK( ctrl.context().setpoints_.position_       == Approx(0.5) );
      // EEPROM
      CHECK( sim().min_position()          == Approx(Utils::Config::servo_absolute_min) );
      CHECK( sim().max_position()          == Approx(Utils::Config::servo_absolute_max) );
      CHECK( sim().EEPROM_LED_brightness() == Approx(Utils::Config::default_LED_brightness).margin(0.01) );
    }

    SECTION("if max < 0.0")
    {
      sim().max_position(-0.1);
      Controller ctrl;
      // sanity checks
      CHECK( ctrl.context().setpoints_.min_pos_  <= ctrl.context().setpoints_.max_pos_  );
      CHECK( ctrl.context().setpoints_.min_pos_  <= ctrl.context().setpoints_.position_ );
      CHECK( ctrl.context().setpoints_.position_ <= ctrl.context().setpoints_.max_pos_  );
      // setpoints
      CHECK( ctrl.context().setpoints_.min_pos_        == Approx(Utils::Config::servo_absolute_min) );
      CHECK( ctrl.context().setpoints_.max_pos_        == Approx(Utils::Config::servo_absolute_max) );
      CHECK( ctrl.context().setpoints_.LED_brightness_ == Approx(Utils::Config::default_LED_brightness).margin(0.01) );
      CHECK( ctrl.context().setpoints_.position_       == Approx(0.5) );
      // EEPROM
      CHECK( sim().min_position()          == Approx(Utils::Config::servo_absolute_min) );
      CHECK( sim().max_position()          == Approx(Utils::Config::servo_absolute_max) );
      CHECK( sim().EEPROM_LED_brightness() == Approx(Utils::Config::default_LED_brightness).margin(0.01) );
    }
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

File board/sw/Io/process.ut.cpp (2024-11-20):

#include "catch2/catch.hpp"
#include "Io/process.hpp"
#include <map>

using Io::Line;
using Io::process;
using namespace Io::Proto;

namespace
{

struct Handler
{
  Get_persistent_config::Reply handle(Get_persistent_config::Request const& req)
  {
    calls_["Get_persistent_config"] += 1;
    return {
      .min_pos_ = 42,
      .max_pos_ = 142,
      .LED_brightness_ = 66
    };
  }

  Get_servo_position::Reply handle(Get_servo_position::Request const& req)
  {
    calls_["Get_servo_position"] += 1;
    return { .pos_{73} };
  }

  Get_telemetry::Reply handle(Get_telemetry::Request const& req)
  {
    calls_["Get_telemetry"] += 1;
    return {
      .eng_current_mA_ = 1234,
      .vcc_voltage_mV_ = 56789
    };
  }

  Ping::Reply handle(Ping::Request const& req)
  {
    calls_["Ping"] += 1;
    return { .pong_ = "YALS test" };
  }

  Set_LED_brightness::Reply handle(Set_LED_brightness::Request const& req)
  {
    calls_["Set_LED_brightness"] += 1;
    return {};
  }

  Set_max_servo_position::Reply handle(Set_max_servo_position::Request const& req)
  {
    calls_["Set_max_servo_position"] += 1;
    return {};
  }

  Set_min_servo_position::Reply handle(Set_min_servo_position::Request const& req)
  {
    calls_["Set_min_servo_position"] += 1;
    return {};
  }

  Set_servo_position::Reply handle(Set_servo_position::Request const& req)
  {
    calls_["Set_servo_position"] += 1;
    return {};
  }

  std::map<std::string, unsigned> calls_;
};


struct ErrorHandler
{
  Get_persistent_config::Reply handle(Get_persistent_config::Request const& req)
  { return { .err_ = "Eget_persistent_configE" }; }

  Get_servo_position::Reply handle(Get_servo_position::Request const& req)
  { return { .err_ = "Eget_servo_positionE" }; }

  Get_telemetry::Reply handle(Get_telemetry::Request const& req)
  { return { .err_ = "Eget_telemetryE" }; }

  Ping::Reply handle(Ping::Request const& req)
  { return { .err_ = "EpingE" }; }

  Set_LED_brightness::Reply handle(Set_LED_brightness::Request const& req)
  { return { .err_ = "Eset_led_brightnessE" }; }

  Set_max_servo_position::Reply handle(Set_max_servo_position::Request const& req)
  { return { .err_ = "Eset_max_servo_positionE" }; }

  Set_min_servo_position::Reply handle(Set_min_servo_position::Request const& req)
  { return { .err_ = "Eset_min_servo_positionE" }; }

  Set_servo_position::Reply handle(Set_servo_position::Request const& req)
  { return { .err_ = "Eset_servo_positionE" }; }
};


auto mk_cmd(std::string_view str, bool append_checksum = true)
{
  Line line;
  for(auto i=0u; i<str.size(); ++i)
    line.add_byte(str[i]);
  if(append_checksum)
    add_checksum(line);
  return line;
}

auto to_string(Line const& line, bool crop_checksum = true)
{
  auto str = std::string{ line.data_.data(), line.data_.data() + line.size_ };
  if( not checksum_valid(line) )
    throw std::runtime_error{"given line has invalid checksum: " + str};
  if(crop_checksum)
    str.resize( str.size() - 2u );
  return str;
}


template<typename H>
auto process_test(std::string_view cmd, H&& h)
{
  auto const c = mk_cmd(cmd);
  auto const l = process(c, h);
  return to_string(l);
}


TEST_CASE("process(): invalid line")
{
  Handler h;
  REQUIRE( h.calls_.empty() );

  SECTION("unkown command")
  {
    CHECK( process_test("xyz", h) == "-unknown cmd" );
    CHECK( h.calls_.empty() );
  }

  SECTION("valid command but checksum is missing")
  {
    CHECK( to_string( process( mk_cmd("@123", false), h ) ) == "-invalid checksum" );
    CHECK( h.calls_.empty() );
  }

  SECTION("valid command but checksum does not match")
  {
    auto line = mk_cmd("?");
    line.data_[line.size_ - 1u] = 'x';
    CHECK( to_string( process(line, h) ) == "-invalid checksum" );
    CHECK( h.calls_.empty() );
  }
}


TEST_CASE("process(): Get_persistent_config")
{
  SECTION("parsing with correct checksum")
  {
    Handler h;
    REQUIRE( h.calls_.empty() );
    CHECK( process_test("?", h) == "+<042>142*66" );
    CHECK( h.calls_.size() == 1 );
    CHECK( h.calls_["Get_persistent_config"] == 1 );
  }

  SECTION("parsing with error handler")
  {
    ErrorHandler h;
    CHECK( process_test("?", h) == "-Eget_persistent_configE" );
  }
}


TEST_CASE("process(): Get_servo_position")
{
  SECTION("parsing with correct checksum")
  {
    Handler h;
    REQUIRE( h.calls_.empty() );
    CHECK( process_test("!", h) == "+073" );
    CHECK( h.calls_.size() == 1 );
    CHECK( h.calls_["Get_servo_position"] == 1 );
  }

  SECTION("parsing with error handler")
  {
    ErrorHandler h;
    CHECK( process_test("!", h) == "-Eget_servo_positionE" );
  }
}


TEST_CASE("process(): Get_telemetry")
{
  SECTION("parsing with correct checksum")
  {
    Handler h;
    REQUIRE( h.calls_.empty() );
    CHECK( process_test("#", h) == "+I1234U56789" );
    CHECK( h.calls_.size() == 1 );
    CHECK( h.calls_["Get_telemetry"] == 1 );
  }

  SECTION("parsing with error handler")
  {
    ErrorHandler h;
    CHECK( process_test("#", h) == "-Eget_telemetryE" );
  }
}


TEST_CASE("process(): Ping")
{
  SECTION("parsing with correct checksum")
  {
    Handler h;
    REQUIRE( h.calls_.empty() );
    CHECK( process_test("~", h) == "+YALS test" );
    CHECK( h.calls_.size() == 1 );
    CHECK( h.calls_["Ping"] == 1 );
  }

  SECTION("parsing with error handler")
  {
    ErrorHandler h;
    CHECK( process_test("~", h) == "-EpingE" );
  }
}


TEST_CASE("process(): Set_LED_brightness")
{
  SECTION("parsing with correct checksum")
  {
    Handler h;
    REQUIRE( h.calls_.empty() );
    CHECK( process_test("*97", h) == "+" );
    CHECK( h.calls_.size() == 1 );
    CHECK( h.calls_["Set_LED_brightness"] == 1 );
  }

  SECTION("parsing with error handler")
  {
    ErrorHandler h;
    CHECK( process_test("*97", h) == "-Eset_led_brightnessE" );
  }
}


TEST_CASE("process(): Set_max_servo_position")
{
  SECTION("parsing with correct checksum")
  {
    Handler h;
    REQUIRE( h.calls_.empty() );
    CHECK( process_test(">997", h) == "+" );
    CHECK( h.calls_.size() == 1 );
    CHECK( h.calls_["Set_max_servo_position"] == 1 );
  }

  SECTION("parsing with error handler")
  {
    ErrorHandler h;
    CHECK( process_test(">997", h) == "-Eset_max_servo_positionE" );
  }
}


TEST_CASE("process(): Set_min_servo_position")
{
  SECTION("parsing with correct checksum")
  {
    Handler h;
    REQUIRE( h.calls_.empty() );
    CHECK( process_test("<321", h) == "+" );
    CHECK( h.calls_.size() == 1 );
    CHECK( h.calls_["Set_min_servo_position"] == 1 );
  }

  SECTION("parsing with error handler")
  {
    ErrorHandler h;
    CHECK( process_test("<321", h) == "-Eset_min_servo_positionE" );
  }
}
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

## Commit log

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2024-03-03 draft of linear potentiometer mock
    [config.scad, lin_pot.scad]
2024-03-03 3D SDK updated to the latest v2.5.0
    [all.scad, math.scad, rounded_cube.scad]
2024-03-03 added 3 connectors in the back - linear potentiometer mock is now complete
    [lin_pot.scad]
2024-03-03 common helper for screw positions
    [lin_pot.scad]
2024-03-03 engine mock from surface drifer
    [config.scad, engine.scad]
2024-03-03 fixed mounts angle + cleaned up source a bit
    [engine.scad]
2024-03-07 parametrized coupler so that it can be incorporated into main design
    [config.scad, coupler.scad]
2024-03-07 placeholder for main servo block
    [servo_body.scad]
2024-03-08 2 more params for engine
    [config.scad, engine.scad]
2024-03-08 initial positioning of servo_body() external elements
    [servo_body.scad]
2024-03-08 setup base elements for servo body
    [config.scad, coupler.scad, servo_body.scad]
2024-03-09 added mockup of a bearing
    [bearing.scad, config.scad]
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2024-03-09 tighter spacing for engine
    [servo_body.scad]
2024-03-09 added mount screw holes for engine top part
    [servo_body.scad]
2024-03-09 added top mount for engine
    [servo_body.scad, servo_body_top_mount.scad]
2024-03-09 added missing engine stiffeners
    [servo_body.scad, servo_body_top_mount.scad]
2024-03-09 fixed wall thickness on top mount
    [servo_body_top_mount.scad]
2024-03-09 fixed engine mount screw positions
    [servo_body.scad, servo_body_top_mount.scad]
2024-03-09 added threaded inserts slots for screws
    [config.scad, servo_body.scad]
2024-03-09 draft of a carriage model
    [carriage.scad, config.scad, servo_body.scad]
2024-03-09 carriage rod position is now properly calculated
    [config.scad, servo_body.scad]
2024-03-09 added proper rod visualization
    [carriage.scad, servo_body.scad]
2024-03-09 carriage is to be printed on its side
    [carriage.scad]
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2024-03-09 fixed fan settings to enable
2024-03-10 fixed linear potentiometer mount screw diameter (M3)
    [config.scad, servo_body.scad]
2024-03-10 carriage is now meant to use 1, long threaded insert insert, instead of 2 screws
    [carriage.scad, config.scad]
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2024-03-13 engine moved extra 3mm backwards, to accomodate for universal joint
    [config.scad, servo_body.scad]
2024-03-13 added a bit extra space for screw to hold potentiometer
    [servo_body.scad]
2024-03-13 used most sizes from the linera's potentiometer datasheet
    [config.scad]
2024-03-17 size + extra size for screws support
    [servo_body.scad]
2024-03-17 added phased support for potentiometed, to avoid touching universal joint
    [servo_body.scad]
2024-03-17 added stiffener for core linear motion support
    [servo_body.scad]
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2024-03-18 latest 3D SDK (dev version)
    [mt44.scad, mt44_conf.scad, mt83.scad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]
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2024-03-21 removed coupler (replaecd by universal joint)
    [config.scad, coupler.scad]
2024-03-21 removed old engine and coupler
    [engine.scad, servo_body.scad]
2024-03-21 universal joint, engine and main rod are now aligned
    [config.scad, servo_body.scad]
2024-03-21 moved potentiometer down a bit
    [config.scad, servo_body.scad]
2024-03-21 smaller supports and and bit thiner walls
    [servo_body.scad]
2024-03-21 upper part of the servo is now ready
    [config.scad, servo_body.scad]
2024-03-21 hilighting was debug only
    [servo_body.scad]
2024-03-21 removed old engine mount blocks
    [config.scad, engine.scad, servo_body.scad]
2024-03-21 removed old code for engine mount
    [servo_body.scad]
2024-03-21 temporary commneted out whole block for top mount
    [servo_body_top_mount.scad]
2024-03-21 removed another unsed param
    [config.scad]
2024-03-21 added helper module for generating common engine slot + slot for real thing on servo body
    [servo_body.scad, servo_body_top_mount.scad]
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2024-03-21 top cover is ready
    [servo_body_top_mount.scad]
2024-03-21 added top cover block
    [servo_body.scad]
2024-03-21 rotated top support for printing
    [servo_body_top_mount.scad]
2024-03-21 around-engine spacing is now properly parametrized
    [config.scad, servo_body.scad, servo_body_top_mount.scad]
2024-03-21 fixed perametrization of rod position in carriage
    [carriage.scad, config.scad, servo_body.scad]
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2024-03-21 added comments on spacing around the engine
    [config.scad]
2024-03-23 * threaded insers have now a tighter slot (as per doc) * engine mount is more tight
    [config.scad]
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2024-03-30 YALS - empty project
    [yals.kicad_pcb, yals.kicad_sch]
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2024-03-30 added schematics with potentiometer
    [yals.kicad_sch]
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2024-03-30 added 2 sub-sheets for µC and power
    [microcontroller.kicad_sch, power.kicad_sch, yals.kicad_pcb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]
2024-03-30 added cristal oscillator with capacitors, and 3.3V LDO voltage regulator
    [microcontroller.kicad_sch, power.kicad_sch, yals.kicad_pcb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]
2024-03-30 power block is almost ready
    [power.kicad_sch, yals.kicad_pcb]
2024-03-30 rp2040 and its connections are nearly done (still missing power-measuring capabilities)
    [engine_ctrl.kicad_sch, microcontroller.kicad_sch, yals.kicad_pcb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]
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2024-03-31 * moved potentiometer to engine's sheet * added engine's Vcc feedback
    [engine_ctrl.kicad_sch, microcontroller.kicad_sch, yals.kicad_pcb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]
2024-03-31 added engine driver with votage measuring resistor to schematics
    [engine_ctrl.kicad_sch, yals.kicad_pcb, yals.kicad_sch]
2024-03-31 fixed feedback pins directions
    [microcontroller.kicad_sch, yals.kicad_pcb, yals.kicad_sch]
2024-03-31 fixed pin directions for engine ctrl and UART
    [microcontroller.kicad_sch, yals.kicad_sch]
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2024-04-07 added board's outer dimensions, placed some more components and added missing power supply slot
    [power.kicad_sch, yals.kicad_pcb]
2024-04-07 fixed OpAmp description wrt gain
    [engine_ctrl.kicad_sch]
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2024-04-07 monior repositioning to avoid PCB edges and better alignment of parallel elements
    [yals.kicad_pcb]
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2024-04-07 added vias to have GND coverage on both layers
    [yals.kicad_pcb]
2024-04-07 fixed 1 DRC cleareance error
    [yals.kicad_pcb]
2024-04-07 increased height of the board by 1mm, to accomodate more wireing that's needed there
    [yals.kicad_pcb]
2024-04-07 fixed all the DRC errors and warning on the PCB
    [yals.kicad_pcb]
2024-04-07 moved power connection a bit higher, to be away from the board
    [yals.kicad_pcb]
2024-04-07 added proper soldermask marking of all I/O pins + moved element designators to rightful places
    [yals.kicad_pcb]
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2024-04-07 added PCB to main servo body visualization as a mock
    [servo_body.scad]
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2024-11-14 model -> body (to make it more meaningful)
    [all.scad, bearing.scad, carriage.scad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]
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2024-11-14 pcb.stl must be ignored - link won't work with docker image
    [pcb.stl]
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2024-11-15 switched to short impolses on the engine
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2024-11-18 ADC test for engine current reworked to use common HAL code
2024-11-18 implementing and tested Sim::reset()
    [sim.ut.cpp]
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2024-11-19 fixed parsing for LED brightness setting
    [process.ut.cpp]
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2024-11-20 fixed marker support in EEPROM
    [Controller.ut.cpp]
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2024-11-20 AI-generated I2C direct I/O (TL;DR fails the same way as all the rest - keeping just for reference)
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2024-11-20 added error handling on writing LED brightness to EEPROM
    [Controller.ut.cpp]
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2024-11-20 setting position now fails with trying to set below min
    [Controller.ut.cpp]
2024-11-20 fixed test for getting presets
    [Controller.ut.cpp]
2024-11-20 fixed Ping's response + UT
    [process.ut.cpp]
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2024-11-21 positioning test (failing now)
    [Engine_controller.ut.cpp]
2024-11-21 updated Engine and sim.ut.cpp to apply correct directions of travel (i.e. consistent with real HW)
    [sim.ut.cpp]
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2024-11-21 fixed all issues with tolerance calculcations
    [Engine_controller.ut.cpp]
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2024-11-21 fixed typo and adjusted TODOs
    [Engine_controller.ut.cpp]
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2024-11-21 fixed UT for max abs value when setting position
    [Handler.ut.cpp]
2024-11-21 added tests for error handling in Controller
    [Controller.ut.cpp]
2024-11-21 adjusted config to produce smooth travel (but susceptible to stall near the edges)
2024-11-21 added simulation of stall + recovery
    [Engine_controller.ut.cpp]
2024-11-22 added test for stalling
    [Engine_controller.ut.cpp]
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2024-11-22 PID reset when preset changes
2024-11-22 added watchdog reset to Controller's main loop
    [Controller.ut.cpp]
2024-11-22 added printing error message on reboot caused by watchdog
2024-11-22 added UT for displaying warning when reboot via watchdog was detected
    [Controller.ut.cpp]
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2024-12-04 added servo mounts, so that it can be screwed into a larger construct
    [config.scad, servo_body.scad]
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2024-12-05 moved pck.stl mock to build/, where it belongs
    [pcb.scad]
2024-12-05 fixed path to pcb.stl
    [pcb.scad]
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2024-12-10 ~WC pin of EEPROM chip is left floating, to make writes possible
    [microcontroller.kicad_sch, yals.kicad_pcb]
2024-12-10 removed unneeded I2C/EEPROM debugging code, that's no longer relevant
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2024-12-12 reworked EEPROM internal interface to use byte arrays and addresses, instead of doign artificail conversions back and forth (sim only for now)
    [Controller.ut.cpp, sim.ut.cpp]
2024-12-12 * added and tested LED-brightness sanitization * added test to ensure all EEPROM values remain as-is, in case there are no issues
    [Controller.ut.cpp]
2024-12-12 * printing test results only on failed test * printing test results in color
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
